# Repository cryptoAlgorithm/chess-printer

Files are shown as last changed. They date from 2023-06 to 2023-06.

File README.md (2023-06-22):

# Chess Printer

> A chess bot, but on steroids.

<p float=left align=middle>
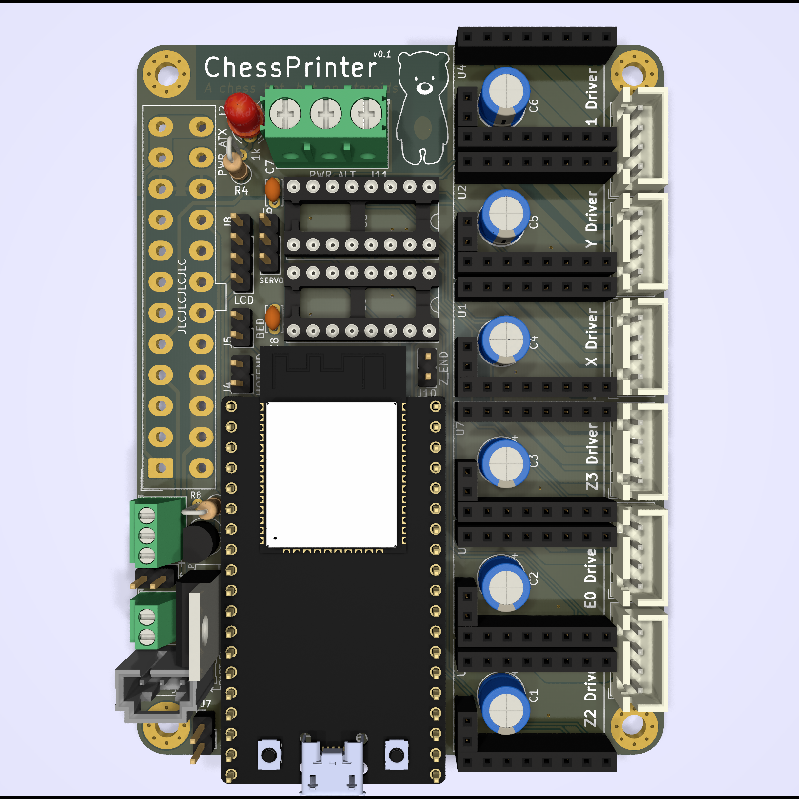
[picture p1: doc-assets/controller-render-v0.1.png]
  
  
</p>

A completely custom-designed 3D printer control board with
an ESP32 MCU. Designed to control a CoreXY printer, but can
probably be adapted to any kinematic system.

> **Warning**: This is an experimental project with no gurantees - use at
> your own risk and discretion!

## Notable Features

* 6 stepper drivers (labelled X, Y, E0, Z1, Z2 & Z3)
  - Designed for TMC2209 drivers
  - 1-wire Serial communication with all drivers supported
* ATX & screw terminal power input
  - `PS-ON` control (standby & emergency kill poweroff supported in Marlin)
  - MCU can be powered from `5VSB` ATX power rail with jumper selection
    (**DO NOT** power via USB and `5VSB` concurrently - doing so will almost definitely damage _something_!)
* ESP32 MCU (DevKit-C footprint)
* I2S stepper stream
  - 2x daisy-chained `75HC595` shift registers
* I2C LCD
* 1 hotend & 1 heatbed thermistor input
* 1 high power MOSFET bed heater & 1 heatbed output (for external relay/SSR)
* 1 controllable & 1 always-on fan output

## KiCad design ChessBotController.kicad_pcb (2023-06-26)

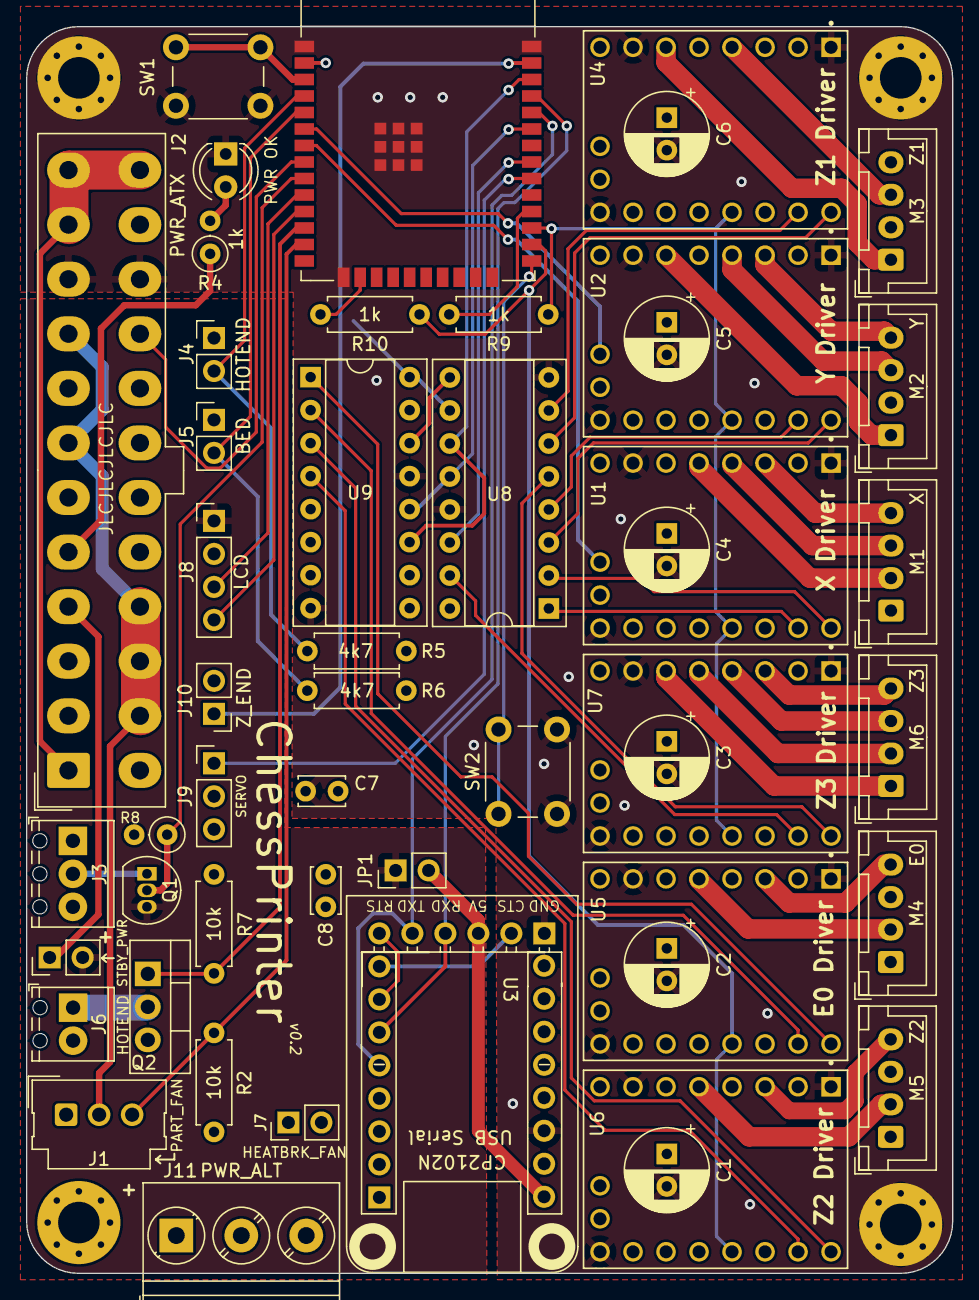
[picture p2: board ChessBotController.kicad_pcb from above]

Board: 4 copper layers, 71.3 x 95.9 mm, 54 parts (0 on the bottom side), 73 nets.

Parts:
C1, C2, C3, C4, C5, C6: 100uF; CP_Radial_D6.3mm_P2.50mm
C7, C8: 0.1uF; C_Disc_D3.4mm_W2.1mm_P2.50mm
D2: PWR OK; LED_D4.0mm
H1, H2, H3, H4: MountingHole_Pad; MountingHole_3.2mm_M3_Pad_Via
J1: PART_FAN; Molex_SL_171971-0003_1x03_P2.54mm_Vertical
J2: PWR_ATX; Molex_Mini-Fit_Jr_ATX24
J3: HEATBED; TerminalBlock_Phoenix_MPT-0,5-3-2.54_1x03_P2.54mm_Horizontal
J4: HOTEND; PinHeader_1x02_P2.54mm_Vertical
J5: BED; PinHeader_1x02_P2.54mm_Vertical
J6: HOTEND; TerminalBlock_Phoenix_MPT-0,5-2-2.54_1x02_P2.54mm_Horizontal
J7: HEATBRK_FAN; PinHeader_1x02_P2.54mm_Vertical
J8: LCD; PinHeader_1x04_P2.54mm_Vertical
J9: SERVO; PinHeader_1x03_P2.54mm_Vertical
J10: Z_END; PinHeader_1x02_P2.54mm_Vertical
J11: PWR_ALT; TerminalBlock_Phoenix_PT-1,5-3-5.0-H_1x03_P5.00mm_Horizontal
JP1: USB_PWR; PinHeader_1x02_P2.54mm_Vertical
JP2: STBY_PWR; PinHeader_1x02_P2.54mm_Vertical
M1: X; JST_XH_B4B-XH-A_1x04_P2.50mm_Vertical
M2: Y; JST_XH_B4B-XH-A_1x04_P2.50mm_Vertical
M3: Z1; JST_XH_B4B-XH-A_1x04_P2.50mm_Vertical
M4: E0; JST_XH_B4B-XH-A_1x04_P2.50mm_Vertical
M5: Z2; JST_XH_B4B-XH-A_1x04_P2.50mm_Vertical
M6: Z3; JST_XH_B4B-XH-A_1x04_P2.50mm_Vertical
Q1: 2N3904; TO-92_Inline
Q2: IRLZ44N; TO-220-3_Vertical
R2, R7: 10k; R_Axial_DIN0207_L6.3mm_D2.5mm_P7.62mm_Horizontal
R4: 1k; R_Axial_DIN0207_L6.3mm_D2.5mm_P2.54mm_Vertical
R5, R6: 4k7; R_Axial_DIN0207_L6.3mm_D2.5mm_P7.62mm_Horizontal
R8: 10K; R_Axial_DIN0207_L6.3mm_D2.5mm_P2.54mm_Vertical
R9, R10: 1k; R_Axial_DIN0207_L6.3mm_D2.5mm_P7.62mm_Horizontal
SW1, SW2: SW_Push; SW_PUSH_6mm
U1, U2, U4, U5, U6, U7: MODULE_TMC2209_SILENTSTEPSTICK
U3: Adafruit-CH2102N-Friend
U8, U9: 74HC595; DIP-16_W7.62mm_Socket
U10: ESP32-WROOM-E; ESP32-WROOM-32E

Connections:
+3.3VP: J2.1 (+3.3V), J2.2 (+3.3V), J2.12 (+3.3V), J2.13 (+3.3V)
+3V3: C7.1, C8.1, R5.1, R6.1, U1.10 (VIO), U2.2 (MS1), U2.10 (VIO), U3.10 (3V3), U4.3 (MS2), U4.10 (VIO), U5.2 (MS1), U5.3 (MS2), U5.10 (VIO), U6.10 (VIO), U7.2 (MS1), U7.10 (VIO), U8.10 (~SRCLR), U8.16 (VCC), U9.10 (~SRCLR), U9.16 (VCC), U10.2 (3V3)
+5V: J8.1, JP1.1 (A), JP2.2 (B), Q1.3 (C)
+5VP: J1.2, J2.4 (+5V), J2.6 (+5V), J2.21 (+5V), J2.22 (+5V), J2.23 (+5V), J9.2, J11.2
+12V: C1.1, C2.1, C3.1, C4.1, C5.1, C6.1, J2.10 (+12V), J2.11 (+12V), J3.1, J6.2, J7.1, J11.1, U1.16 (VM), U2.16 (VM), U4.16 (VM), U5.16 (VM), U6.16 (VM), U7.16 (VM)
/BED_H: Q1.2 (B), R8.1, U10.9 (32K_XN/GPIO33/ADC1_CH5)
/DRIVER_UART_1: R9.2, U1.5 (TX), U2.5 (TX), U4.5 (TX), U7.5 (TX), U10.27 (GPIO16)
/DRIVER_UART_2: R10.2, U5.5 (TX), U6.5 (TX), U10.26 (ADC2_CH0/GPIO4)
/E_DIR: U5.8 (DIR), U9.1 (QB)
/E_STEP: U5.7 (STEP), U9.2 (QC)
/FAN_0: J1.3, R2.1, U10.13 (MTMS/GPIO14/ADC2_CH6)
/HOTEND_H: Q2.1 (G), R7.1, U10.12 (ADC2_CH7/GPIO27)
/I2S_BCK: U8.11 (SRCLK), U9.11 (SRCLK), U10.36 (GPIO22)
/I2S_DIN: U8.14 (SER), U10.31 (GPIO19)
/I2S_WCK: U8.12 (RCLK), U9.12 (RCLK), U10.33 (GPIO21)
/MCU_RXD: U3.5 (TXD), U3.20 (TXD), U10.34 (U0RXD/GPIO3)
/MCU_TXD: U3.4 (RXD), U3.19 (RXD), U10.35 (U0TXD/GPIO1)
/PS_ON: J2.16 (PS_ON#), U10.8 (32K_XP/GPIO32/ADC1_CH4)
/Power/PWR_OK: J2.8 (PWR_OK), R4.1
/SCL: J8.3, U10.10 (DAC_1/ADC2_CH8/GPIO25)
/SDA: J8.4, U10.11 (DAC_2/ADC2_CH9/GPIO26)
/SERVO: J9.1, U10.30 (GPIO18)
/TEMP_BED: J5.2, R6.2, U10.5 (SENSOR_VN/GPIO39/ADC1_CH3)
/TEMP_HOTEND: J4.2, R5.2, U10.4 (SENSOR_VP/GPIO36/ADC1_CH0)
/X_DIR: U1.8 (DIR), U8.2 (QC)
/X_MIN: U1.17 (DIAG), U10.7 (GPIO35/ADC1_CH7)
/X_STEP: U1.7 (STEP), U8.1 (QB)
/Y_DIR: U2.8 (DIR), U8.3 (QD)
/Y_MIN: U2.17 (DIAG), U10.6 (GPIO34/ADC1_CH6)
/Y_STEP: U2.7 (STEP), U8.4 (QE)
/Z2_DIR: U6.8 (DIR), U9.3 (QD)
/Z2_STEP: U6.7 (STEP), U9.4 (QE)
/Z3_DIR: U7.8 (DIR), U8.5 (QF)
/Z3_STEP: U7.7 (STEP), U8.15 (QA)
/Z_DIR: U4.8 (DIR), U8.6 (QG)
/Z_MIN: J10.1, U10.37 (GPIO23)
/Z_STEP: U4.7 (STEP), U8.7 (QH)
GND: C1.2, C2.2, C3.2, C4.2, C5.2, C6.2, C7.2, C8.2, D2.1 (K), H1.1, H2.1, H3.1, H4.1, J1.1, J2.3 (GND), J2.5 (GND), J2.7 (GND), J2.15 (GND), J2.17 (GND), J2.18 (GND), J2.19 (GND), J2.24 (GND), J3.3, J4.1, J5.1, J7.2, J8.2, J9.3, J10.2, J11.3, Q2.3 (S), R2.2, R7.2, R8.2, SW1.1, SW2.2, U1.1 (EN), U1.9 (GND), U1.15 (GND), U2.1 (EN), U2.9 (GND), U2.15 (GND), U3.1 (GND), U3.11 (GND), U4.1 (EN), U4.9 (GND), U4.15 (GND), U5.1 (EN), U5.9 (GND), U5.15 (GND), U6.1 (EN), U6.9 (GND), U6.15 (GND), U7.1 (EN), U7.9 (GND), U7.15 (GND), U8.8 (GND), U8.13 (~OE), U9.8 (GND), U9.13 (~OE), U10.1 (GND), U10.15 (GND), U10.38 (GND), U10.39 (GND_THERMAL)
unnamed: D2.2 (A), R4.2
unnamed: J2.9 (+5VSB), JP2.1 (A)
unnamed: J3.2, Q1.1 (E)
unnamed: J6.1, Q2.2 (D)
unnamed: JP1.2 (B), U3.3 (5V), U3.9 (5V)
unnamed: M1.2 (-), U1.13 (A1)
unnamed: M2.2 (-), U2.13 (A1)
unnamed: M3.2 (-), U4.13 (A1)
unnamed: M4.2 (-), U5.13 (A1)
unnamed: M5.2 (-), U6.13 (A1)
unnamed: M6.2 (-), U7.13 (A1)
unnamed: M1.1, U1.14 (A2)
unnamed: M1.3, U1.12 (B1)
unnamed: M1.4, U1.11 (B2)
unnamed: M2.1, U2.14 (A2)
unnamed: M2.3, U2.12 (B1)
unnamed: M2.4, U2.11 (B2)
unnamed: U3.8 (RTS), U3.18 (RTS)
unnamed: M3.1, U4.14 (A2)
unnamed: M3.3, U4.12 (B1)
unnamed: M3.4, U4.11 (B2)
unnamed: M4.1, U5.14 (A2)
unnamed: M4.3, U5.12 (B1)
unnamed: M4.4, U5.11 (B2)
unnamed: M5.1, U6.14 (A2)
unnamed: M5.3, U6.12 (B1)
unnamed: M5.4, U6.11 (B2)
unnamed: M6.1, U7.14 (A2)
unnamed: M6.3, U7.12 (B1)
unnamed: M6.4, U7.11 (B2)
unnamed: U8.9 (QH'), U9.14 (SER)
unnamed: SW1.2, U10.3 (EN/CHIP_PU)
unnamed: SW2.1, U10.25 (GPIO0/BOOT/ADC2_CH1)
unnamed: R9.1, U10.28 (GPIO17)
unnamed: R10.1, U10.16 (MTCK/GPIO13/ADC2_CH4)

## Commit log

2023-05-25 feat: initial commit
    [ChessBotController copy.kicad_pcb, ChessBotController.kicad_pcb, ChessBotController.kicad_sch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]
2023-06-22 patch(gitignore): make backup ignore rule more specific
    patch: remove redundant copy of PCB with old design
    [ChessBotController copy.kicad_pcb]
2023-06-22 feat(README): upload assembled controller image
2023-06-26 feat: initial v0.2 design
    [ChessBotController.kicad_pcb, ChessBotController.kicad_sch, pwr.kicad_sch]
